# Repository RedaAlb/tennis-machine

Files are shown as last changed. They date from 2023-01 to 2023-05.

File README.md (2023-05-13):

 # Tennis Machine

Current tennis machines only launch balls at random or pre-set fixed positions, which does not provide a realistic or practical training experience. In this project, I am making a tennis ball launcher machine that imitates human playing behaviour, by analysing and tracking court and player data using an on-board camera to recognise the most realistic reply shot that resembles a real tennis player.

The project is in initial development and experimentation stages, more details will be added as the project evolves.

# Current state

The machine can successfully launch balls anywhere on the court with specific speed, top spin, and back spin.



# Components

- [ESP32](https://amzn.eu/d/78Lzigs), for the micro-controller, see `/arduino` for more details.
- [DC Motor 24V 150W 5500RPM](https://amzn.eu/d/2Lb6XL5) (x2), to spin the two wheels to launch balls.
- [BTS7960 DC Motor driver 43A](https://amzn.eu/d/ffBzzgu) (x2), to control the DC motors using the micro-controller.
- [Lipo 3S 11.1V battery](https://amzn.eu/d/eeGYmOE), powers supply.
- [Voltage regulator 12V-24V 10A](https://amzn.eu/d/7cRRwgR), to convert battery 11.1V to 24V for the DC motors.
- [TFT 2.8 LCD touch screen](https://amzn.eu/d/0zSkMGs), to control the machine.
- Plywood 12mm, for the frame.
- 3D printed wheels, to launch the balls, please refer to the `/3d_printing` directory.

# Schematic

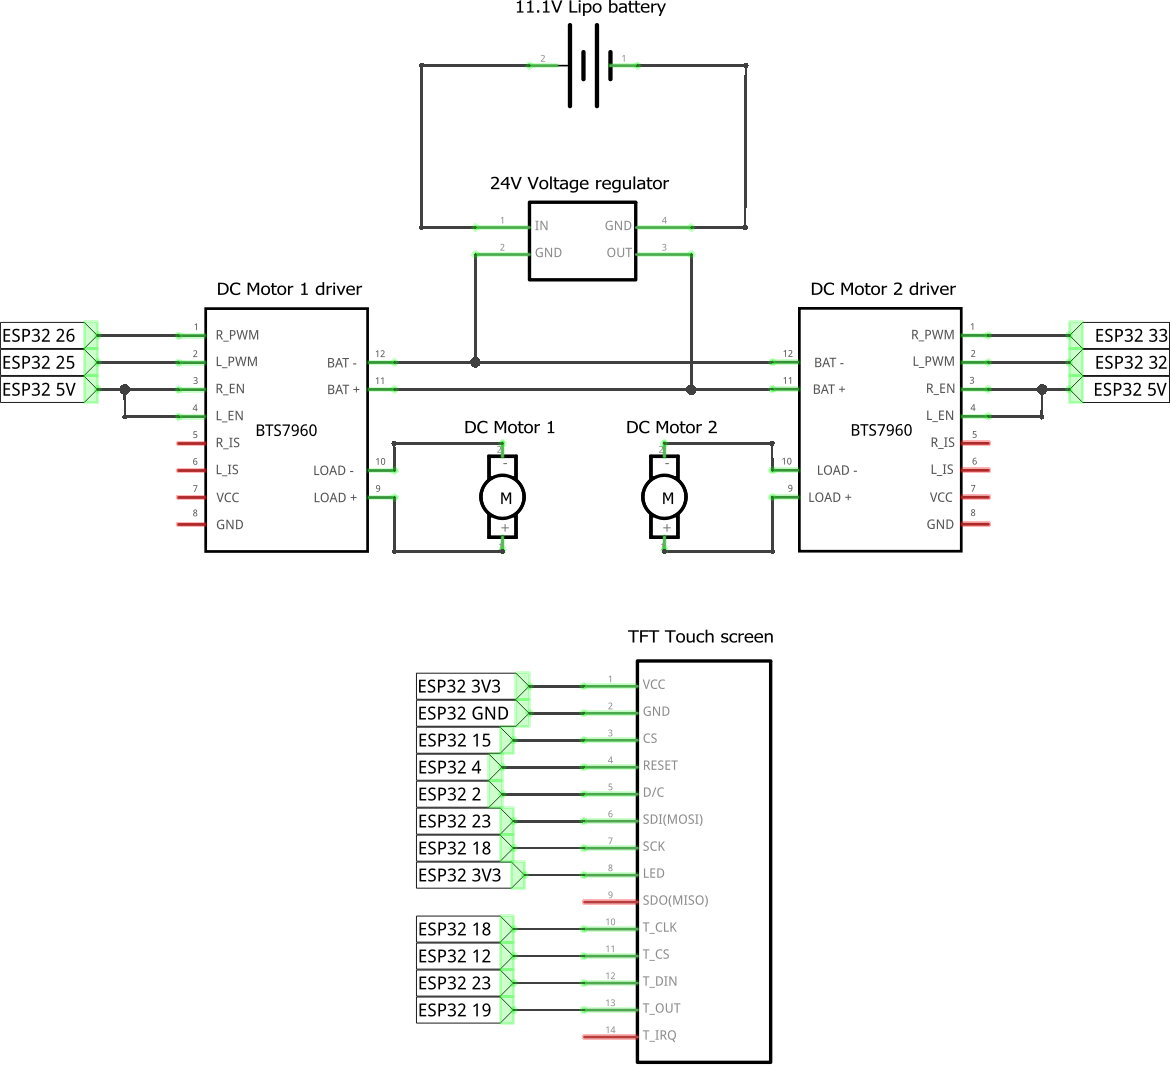
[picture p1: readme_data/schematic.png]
schematic


# Assembly

| CAD design | Assembly |
|---|---|
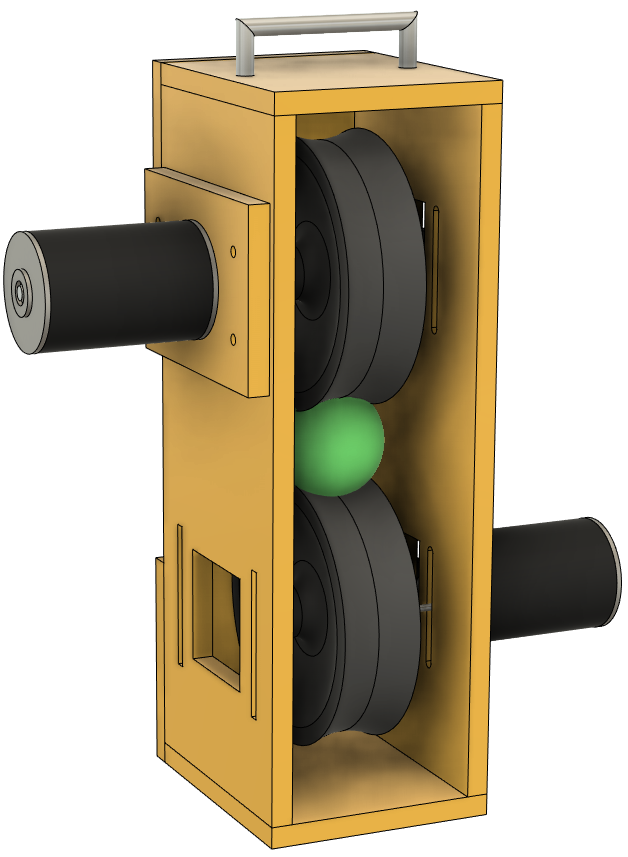
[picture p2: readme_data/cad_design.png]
cad_design
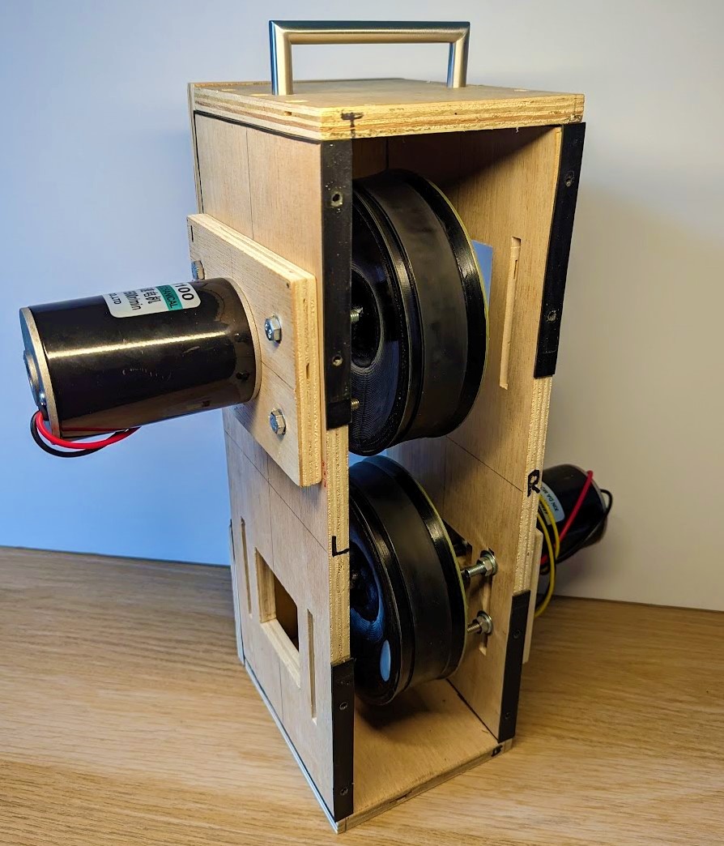
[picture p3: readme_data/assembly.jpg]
assembly
|  |  |

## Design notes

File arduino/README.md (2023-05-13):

# Libraries required

- `TFT_eSPI` by Bodmer.
- `TFT_eWidget` by Bodmer.

# Structure

- `ESP32.ino`, main Arduino sketch.
- `LauncherMotors.ino`, two dc motors to launch the tennis balls.
- `TFTScreen.ino`, TFT screen to get touch input from the user.
- `Free_Fonts.h`, provided by the `TFT_eSPI` library.

# TFT screen

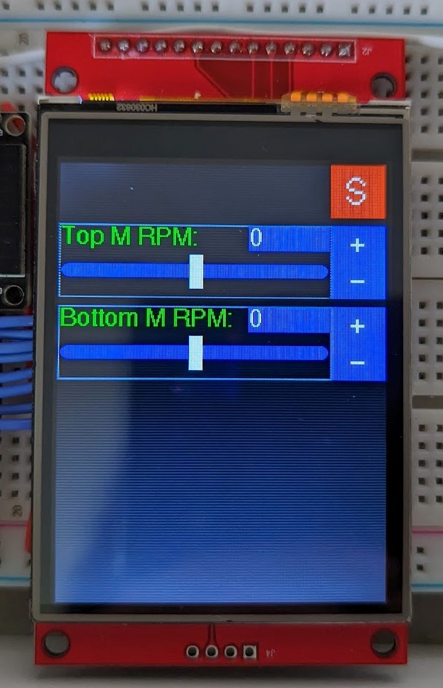
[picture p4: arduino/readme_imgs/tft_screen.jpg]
tft_screen


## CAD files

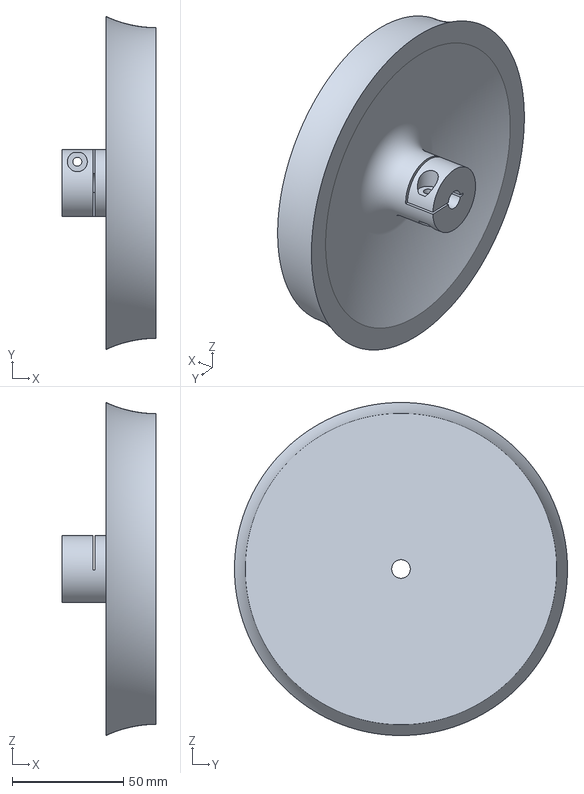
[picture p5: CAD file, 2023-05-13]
3d_printing/wheel_half.3mf
42.5 x 150.0 x 150.0 mm

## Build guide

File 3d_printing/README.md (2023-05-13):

# 3D printing

## Wheel

- `wheel_half.3mf`
- To make the wheels stronger and have an efficient printing time, the wheel is made up of two identical parts, these parts are simply glued together to form a full wheel.
- PETG filament is used for maximum strength.
- For the printing settings, please refer to `readme_data/wheel_printing_settings.curaprofile`.

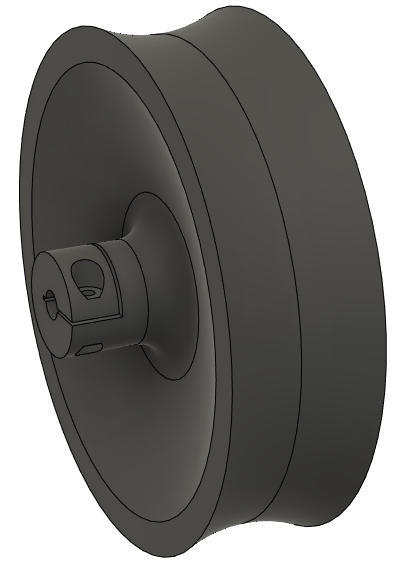
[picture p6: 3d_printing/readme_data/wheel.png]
wheel


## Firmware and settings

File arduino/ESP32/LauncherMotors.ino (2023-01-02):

// Launcher motors, top and bottom.
const int MOTOR_T_PWM1_PIN = 32;  // T = top, forward direction.
const int MOTOR_T_PWM2_PIN = 33;  // Backward direction.

const int MOTOR_B_PWM1_PIN = 25;  // B = bottom
const int MOTOR_B_PWM2_PIN = 26;


const int MOTORS_MIN_RPM = 0;
const int MOTORS_MAX_RPM = 7000;


const int MOTOR_T_PWM1_CHANNEL = 1;
const int MOTOR_T_PWM2_CHANNEL = 2;
const int MOTOR_B_PWM1_CHANNEL = 3;
const int MOTOR_B_PWM2_CHANNEL = 4;
const int MOTORS_PWM_FREQ = 2000;
const int MOTORS_PWM_BITS = 12;


// Integers to represent top and bottom launcher motors.
const int LAUNCHER_TOP_MOTOR = 0;
const int LAUNCHER_BOT_MOTOR = 1;


// Current launcher motors rpm, top and bottom.
int motorTopRpm = 0;
int motorBotRpm = 0;


/// @brief Initialise motors pulse-width modulation (PWM) signals.
void initLauncherMotors() {
    // Top motor
    ledcSetup(MOTOR_T_PWM1_CHANNEL, MOTORS_PWM_FREQ, MOTORS_PWM_BITS);
    ledcAttachPin(MOTOR_T_PWM1_PIN, MOTOR_T_PWM1_CHANNEL);
    ledcSetup(MOTOR_T_PWM2_CHANNEL, MOTORS_PWM_FREQ, MOTORS_PWM_BITS);
    ledcAttachPin(MOTOR_T_PWM2_PIN, MOTOR_T_PWM2_CHANNEL);

    // Bottom motor
    ledcSetup(MOTOR_B_PWM1_CHANNEL, MOTORS_PWM_FREQ, MOTORS_PWM_BITS);
    ledcAttachPin(MOTOR_B_PWM1_PIN, MOTOR_B_PWM1_CHANNEL);
    ledcSetup(MOTOR_B_PWM2_CHANNEL, MOTORS_PWM_FREQ, MOTORS_PWM_BITS);
    ledcAttachPin(MOTOR_B_PWM2_PIN, MOTOR_B_PWM2_CHANNEL);
}


/// @brief Handle the top and bottom launcher dc motors.
void handleLauncherMotors() {
    setLauncherMotorSpeed(LAUNCHER_TOP_MOTOR, motorTopRpm);
    setLauncherMotorSpeed(LAUNCHER_BOT_MOTOR, motorBotRpm);
}


/// @brief Set the speed and spin direction of launcher motor.
/// @param motor The motor to control, 0 = top motor, 1 = bottom motor.
/// @param rpm The speed of the motor, (+rpm = forward, -rpm = backward).
void setLauncherMotorSpeed(int motor, int rpm) {
    int pwmSignal = map(abs(rpm), MOTORS_MIN_RPM, MOTORS_MAX_RPM, 0, pow(2, MOTORS_PWM_BITS));

    int motorPwmChannel1, motorPwmChannel2;

    if (motor == 0) {
        motorPwmChannel1 = MOTOR_T_PWM1_CHANNEL;
        motorPwmChannel2 = MOTOR_T_PWM2_CHANNEL;
    }
    else if (motor == 1) {
        motorPwmChannel1 = MOTOR_B_PWM1_CHANNEL;
        motorPwmChannel2 = MOTOR_B_PWM2_CHANNEL;
    }

    if (rpm > 0) {
        ledcWrite(motorPwmChannel1, pwmSignal);
        ledcWrite(motorPwmChannel2, 0);
    }
    else if (rpm < 0) {
        ledcWrite(motorPwmChannel1, 0);
        ledcWrite(motorPwmChannel2, pwmSignal);
    }
    else {
        ledcWrite(motorPwmChannel1, 0);
        ledcWrite(motorPwmChannel2, 0);
    }
}

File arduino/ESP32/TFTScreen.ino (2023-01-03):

#include <TFT_eSPI.h>
#include <TFT_eWidget.h>
#include "FS.h"
#include "Free_Fonts.h"


TFT_eSPI tft = TFT_eSPI();
TFT_eSprite knob = TFT_eSprite(&tft);
SliderWidget sw = SliderWidget(&tft, &knob);


typedef struct {
    int x, y, w, h;
    String text;
    int textC, bgC;
} Button;

typedef struct {
    int x, y, minValue, maxValue, & value, step;
    bool useMidpoint;  // To make slider middle value 0, with either side +-maxValue.
    String name;
    Button btn1;
    Button btn2;
    SliderWidget slider;
} Slider;


Slider SLIDERS[]{
    {0, 45, MOTORS_MIN_RPM, MOTORS_MAX_RPM, motorTopRpm, 100, true, "Top M RPM:", {}, {}, sw},
    {0, 105, MOTORS_MIN_RPM, MOTORS_MAX_RPM, motorBotRpm, 100, true, "Bottom M RPM:", {}, {}, sw},
};


// Button to stop all motors.
Button stopMotorsBtn = { 199, 0, 40, 39, "S", TFT_WHITE, TFT_RED };
bool stopMotors = false;  // If set to true, it will gradually stop all motors.
unsigned long prevMillies = 0;
const int STOP_MOTORS_DELAY = 10;  // How long to wait between each deceleration step in milliseconds.

uint16_t tX = 9999, tY = 9999;  // To store the touch coordinates.
unsigned long tftScanTime = 0;


// Function declarations are needed here because of the arduino ide auto-prototype generation.
void makeSlider(Slider& slider);
void drawSliderValue(Slider& slider);
void setSliderValue(Slider& slider, int newValue);
void drawButton(Button& btn);
bool buttonClicked(Button& btn);


/// @brief Setup TFT screen and draw initial ui.
void initTFTScreen() {
    tft.begin();
    tft.setRotation(2);

    // Obtain numbers below by calibrating your tft screen, see TFT_eSPI library examples.
    uint16_t calData[5] = { 324, 3415, 445, 3464, 2 };
    tft.setTouch(calData);

    tft.fillScreen(TFT_BLACK);
    tft.setFreeFont(FF17);

    drawUi();
}


/// @brief Draw the static UI on the TFT screen.
void drawUi() {
    drawControlsView();
}


/// @brief Draw the controls needed to control the machine manually.
void drawControlsView() {
    drawButton(stopMotorsBtn);

    int numOfSliders = sizeof(SLIDERS) / sizeof(SLIDERS[0]);

    for (int i = 0; i < numOfSliders; i++) {
        makeSlider(SLIDERS[i]);
    }
}


/// @brief Draw the slider value based on slider location.
/// @param slider The slider to display the value of.
void drawSliderValue(Slider& slider) {
    tft.setTextColor(TFT_WHITE, TFT_BLUE);
    tft.setTextSize(1);
    tft.setTextPadding(60);
    tft.drawNumber(slider.value, slider.x + 139, slider.y + 1);
    tft.setTextPadding(0);
}


/// @brief Draw a button.
/// @param btn The button struct to draw.
void drawButton(Button& btn) {
    tft.fillRect(btn.x, btn.y, btn.w, btn.h, btn.bgC);
    tft.setTextColor(btn.textC);
    tft.setTextSize(2);
    tft.setTextDatum(MC_DATUM);
    tft.drawString(btn.text, btn.x + (btn.w / 2), btn.y + (btn.h / 2), 2);
    tft.setTextDatum(TL_DATUM);
}


/// @brief Make a slider and draw it.
/// @param slider The slider struct to draw.
void makeSlider(Slider& slider) {
    // Slider text
    tft.setTextColor(TFT_GREEN, TFT_BLACK);
    tft.setTextSize(1);
    tft.drawString(slider.name, slider.x + 1, slider.y + 1);

    drawSliderValue(slider);


    // Slider parameters
    slider_t param;

    param.slotWidth = 10;
    param.slotLength = 196;
    param.slotColor = TFT_BLUE;
    param.slotBgColor = TFT_BLACK;
    param.orientation = H_SLIDER;

    param.knobWidth = 10;
    param.knobHeight = 25;
    param.knobRadius = 0;
    param.knobColor = TFT_WHITE;
    param.knobLineColor = TFT_WHITE;

    param.sliderDelay = 0;

    param.sliderLT = slider.minValue;
    param.sliderRB = slider.maxValue;
    param.startPosition = 0;

    slider.slider.drawSlider(slider.x, slider.y + 20, param);


    // For slider bounding box.
    int16_t bb_x, bb_y;
    uint16_t bb_w, bb_h;
    slider.slider.getBoundingRect(&bb_x, &bb_y, &bb_w, &bb_h);
    tft.drawRect(slider.x, slider.y, bb_w, bb_h + param.knobHeight, TFT_DARKGREY);


    // Slider increment buttons.
    int btns_w = 40;
    int btns_h = 27;
    Button btn1 = { param.slotLength + 4, slider.y, btns_w, btns_h, "+", TFT_WHITE, TFT_BLUE };
    Button btn2 = { param.slotLength + 4, slider.y + btns_h, btns_w, btns_h, "-", TFT_WHITE, TFT_BLUE };

    drawButton(btn1);
    drawButton(btn2);

    slider.btn1 = btn1;
    slider.btn2 = btn2;

    setSliderValue(slider, slider.value);
}


/// @brief Check if a button is clicked or not.
/// @param btn The button to check.
/// @return A boolean whether the button is pressed or not.
bool buttonClicked(Button& btn) {
    if ((tX > btn.x) && (tX < (btn.x + btn.w))) {
        if ((tY > btn.y) && (tY <= (btn.y + btn.h))) {
            return true;
        }
    }

    return false;
}


/// @brief Set a new slider value.
/// @param slider The slider to change value of.
/// @param newValue The new slider value.
void setSliderValue(Slider& slider, int newValue) {
    if (newValue > slider.maxValue ||
        (!slider.useMidpoint && newValue < slider.minValue) ||
        (slider.useMidpoint && newValue < -slider.maxValue)) {
        return;
    }

    slider.value = newValue;
    int sliderPos = newValue;

    if (slider.useMidpoint) {
        // Convert the slider value (-maxValue to maxValue) to a slider position.
        sliderPos = (newValue / 2) + (slider.maxValue / 2);
    }

    slider.slider.setSliderPosition(sliderPos);

    drawSliderValue(slider);
}


/// @brief Gradually reset all sliders to a value of 0, to prevent braking current spike.
void resetSliderValues() {
    int numOfSliders = sizeof(SLIDERS) / sizeof(SLIDERS[0]);

    if ((millis() - prevMillies) > STOP_MOTORS_DELAY) {
        for (int i = 0; i < numOfSliders; i++) {
            if (SLIDERS[i].value == 0) {
                continue;
            }

            if (SLIDERS[i].value > 0) {
                setSliderValue(SLIDERS[i], SLIDERS[i].value - SLIDERS[i].step);
            }
            if (SLIDERS[i].value < 0) {
                setSliderValue(SLIDERS[i], SLIDERS[i].value + SLIDERS[i].step);
            }
        }
        prevMillies = millis();
    }
}
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

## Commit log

2022-12-08 Use TFT touch screen to control dc motors.
2022-12-09 Add launcher motors spin direction control using tft screen +-slider.
2022-12-09 Add stop all motors button.
2023-01-02 Use bts7960 motor driver instead of l298N for launcher motors.
2023-01-03 Add motor deceleration for stop button.
2023-05-13 Update readme files, add components and more details.
    [wheel_half.3mf]
